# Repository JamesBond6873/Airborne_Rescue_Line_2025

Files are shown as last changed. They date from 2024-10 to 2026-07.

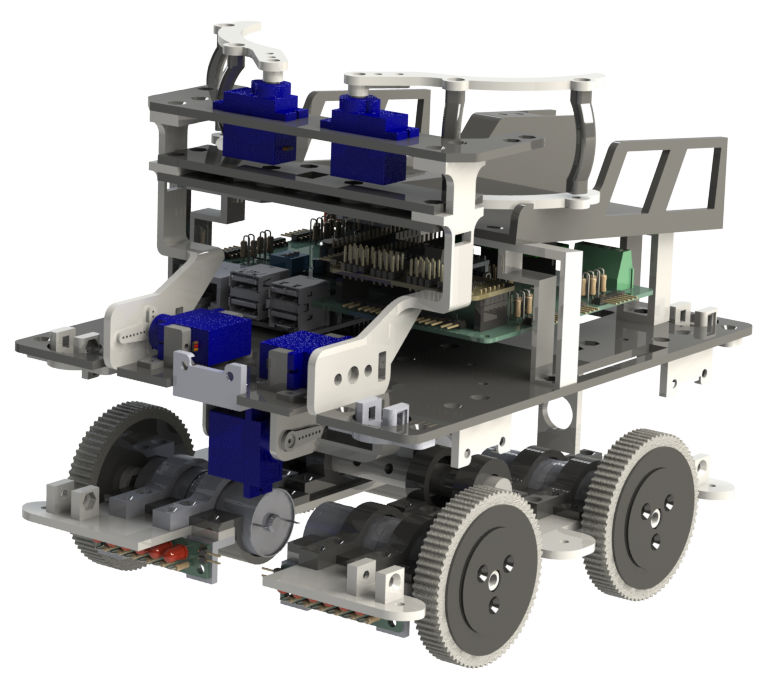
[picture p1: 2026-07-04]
Hardware/CAD/3D_Model_Pictures/Wall-E_3D_Model_Right.png

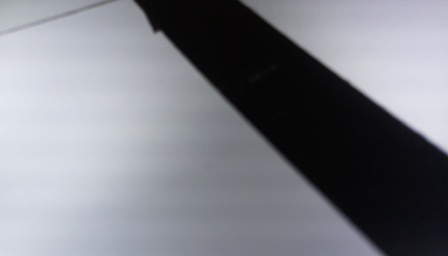
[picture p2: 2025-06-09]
SwTest/Image (122).jpg

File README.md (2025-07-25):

<div align="center">
  <a href="https://github.com/JamesBond6873">
    
  </a>
  
  <a href="https://github.com/eumesmodefacto">
    
  </a>
</div>

<br/>

<p align="center">
  This is the repository for <strong>Airborne</strong>, a Portuguese robotics team that participated in the
  <a href="https://junior.robocup.org/">RoboCup Junior</a> sub-league
  <a href="https://junior.robocup.org/rcj-rescue-line/">Rescue Line</a>.
</p>

# About the Competition
<p align="center"><i>
  "The land is too dangerous for humans to reach the victims. Your team has been given a challenging task. The robot must be able to carry out a rescue mission in a fully autonomous mode with no human assistance. The robot must be durable and intelligent enough to navigate treacherous terrain with hills, uneven land, and rubble without getting stuck. When the robot reaches the victims, it has to gently and carefully transport each one to the safe evacuation point where humans can take over the rescue. The robot should exit the evacuation zone after a successful rescue to continue its mission throughout the disaster scene until it leaves the site. Time and technical skills are essential!"
</i></p>

<div align="center">
  
</div>

# About the Robot

<!-- First block: Image on the left -->


<p align="justify">
  Our robot was built to reliably complete all challenges of the RoboCup Junior Rescue Line competition through a combination of computation, custom electronics, and mechanical design. It uses a dual-processor architecture: a Raspberry Pi 5 for high-level logic and AI, and a Raspberry Pi Pico for real-time control of motors and sensors. A Google Coral USB Accelerator enables onboard execution of two YOLOv8 models, one for victim detection and another for identifying the silver evacuation zone, which provide fast and accurate results compared to traditional computer vision.
</p>

<br/>

<!-- Second block: Image on the right -->


<p align="justify">
  The chassis was entirely designed in SolidWorks and 3D printed, with over 70 custom parts and a modular structure that simplifies maintenance. A tilt-mounted wide-angle camera, passive suspension system, and dual-servo rescue arm ensure strong performance across rough terrain. Internally, custom PCBs manage power distribution and sensor integration, keeping the system reliable and clean, with a much lower risk of lose wires. Software processes run in parallel for serial communication between boards, image processing, and control/decision-making, supported by a custom HTML/Websocket interface for real-time monitoring and debugging.
</p>

<br/>

<p align="center">
  As required by the competition <a href="https://github.com/JamesBond6873/Airborne_Rescue_Line_2025/blob/main/Documents/Rules/000_RoboCup_Junior_Rescue_Line_Rules_2025.pdf">rules</a>, in addition to this GitHub Repository, we created detailed documentation of the robot and our development process in the form of a <a href="https://github.com/JamesBond6873/Airborne_Rescue_Line_2025/blob/main/Documents/Final%20Rubrics/00_Airborne_TDP_RoboCup_Rescue_Line_2025.pdf">Technical Description Paper</a>, a <a href="https://github.com/JamesBond6873/Airborne_Rescue_Line_2025/blob/main/Documents/Final%20Rubrics/01_Airborne_Poster_RoboCup_Rescue_Line_2025.pdf">Technical Poster</a>, and a <a href="https://github.com/JamesBond6873/Airborne_Rescue_Line_2025/blob/main/Documents/Final%20Rubrics/02_Airborne_Video_RoboCup_Rescue_Line_2025_Compressed.mp4">Presentation Video</a>.
</p>

## 📂 Components

- Raspberry Pi 5 8GB Ram
- Raspberry Pi Pico
- Google Coral USB Accelerator
- Raspberry Pi Camera Module V3 Wide
- 5x VL53L0X ToF
- ICM-20948 9DOF IMU
- TCA9458 Multiplexer
- 4x Home-made Silicone Wheels
- 4x 12V 77RPM DC Geared Motors
- 4x 3S ESCs
- 6x SG90 MicroServos
- PCA9685 Servo Driver
- 2x Custom Led Bar PCB
- DRV8833 Power Driver
- Gens Ace 3S 2700mAh Lipo Battery
- D24V50F5 Step Down
- D36V28F5 Step Down

<br/>

## 🧠 Repository Structure

<p align="justify"> 
  This repository contains all the files developed and used throughout our RoboCup Junior Rescue Line project.
</p>

  - <code>RobotCode_Field_Version</code>: Contains the latest version of the code used in the official Field Runs
  - <code>RobotCode_TC_Version</code>: Contains the version used during the Technical Challenge run
  - <code>Ai</code>: Contains the versions of the YoloV8 Small Models used for victim and silver strip detections
  - <code>Documents</code>:
      - <code>Final Rubrics</code>: Contains our final three evaluated documents: Team Description Paper, Technical Poster and  Presentation Video (compressed)
      - <code>Rules</code>: Contains all official competition rulebooks (Rescue Line, Technical Challenge, SuperTeams), as well as the corresponding rubrics and templates for the documents
      - <code>scores</code>:  Contains the final scores from the RoboCup Junior World Championship 2025, in Salvador, Brazil

<br/>

# 🔗 Useful Links

- [Airborne Photo/Video Album](https://drive.google.com/drive/folders/1JC7H4FIJUuHvwdzJ9MUNMwsvkezMXKDg?usp=drive_link)
- [Technical Description Paper](https://drive.google.com/file/d/1SsVflj773ZcgajpcdkzmWjwUXBWZYv1-/view?usp=drive_link)
- [Technical Poster](https://drive.google.com/file/d/1fPJXqmR9CHxOLH45z3VVppOXiR5PiPfq/view?usp=drive_link)
- [Presentation Video](https://drive.google.com/file/d/1rCQD-FLG8RNpqSPlJDvGeZCaVhfCN_2y/view?usp=drive_link)
- [Rescue Line Rules 2025](https://github.com/JamesBond6873/Airborne_Rescue_Line_2025/blob/main/Documents/Rules/000_RoboCup_Junior_Rescue_Line_Rules_2025.pdf)
- [Airborne Instagram Account](https://www.instagram.com/airborne_2023/)

<br/>
<br/>

# 🤝 Sponsors



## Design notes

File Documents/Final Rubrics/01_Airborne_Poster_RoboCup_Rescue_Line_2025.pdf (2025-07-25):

# Team

## Team Captain; Lead Programmer; Electronics & PCB Design; Ai

## Francisco Gaspar

I’m Francisco, and I’ve been leading the team since the start in 2022. I designed our custom PCBs and handled most of the programming, from low-level control to AI integration. I trained and deployed our YOLOv8 models and built the logic that helps the robot make decisions on the field. I love solving problems by mixing hardware and software.

## André Pinto

## Team Co-Captain; 3D modelling; Sponsorship Manager

I’m André, and I focused on designing the robot’s structure. I created all the 3D models in SolidWorks and made sure everything, from suspension to the camera tilt mechanism, fit and worked reliably. I also took care of getting sponsorships and managing our budget. I really enjoy the mechanical side of things and making sure we’re prepared both on and off the field.

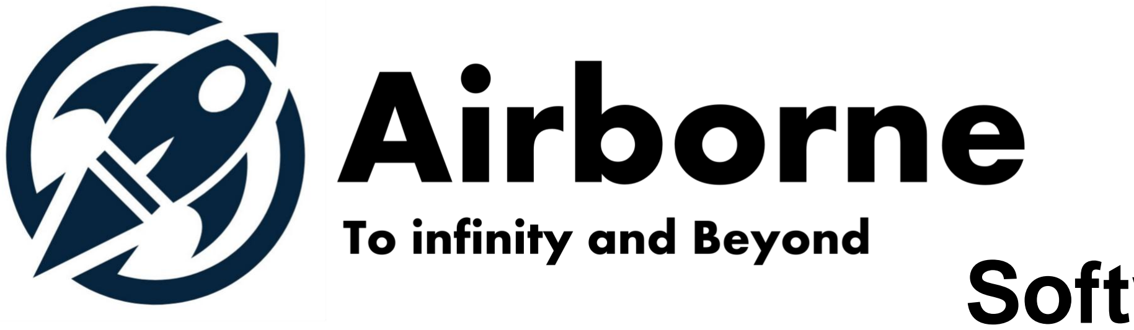
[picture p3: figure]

Airborne Robotics was founded in 2023 with the goal of building a CanSat for the national competition. Nevertheless, we ended up competing
in | our | first | Robotics | National
Championship (FNR 2024), securing 1

st Place and qualifying for the European Championship in Germany. Although our results weren’t perfect,
the | experience | motivated | us | to
completely redesign the robot from the ground up. In 2025, with a new dual-processor architecture and our first reliable custom PCBs, we won 1st place at the National Championship Rescue Line Competition, earning us a
spot | at | the | RoboCup | World
Championship in Brazil.

European Championship 2024

National Robotics Festival 2025

1

st Place FNR 2024

1

st Place FNR 2025

## Raspberry Pi Pico

Chosen for its versatility and general compatibility; responsible for sensor and actuator integration

## Raspberry Pi 5

Main computing device,
responsible for image
processing and decision
making

## Raspberry Pi Camera Module V3 Wide

Used to acquire visual
data; main sensor

## TCA9458 Multiplexer

Responsible for integrating

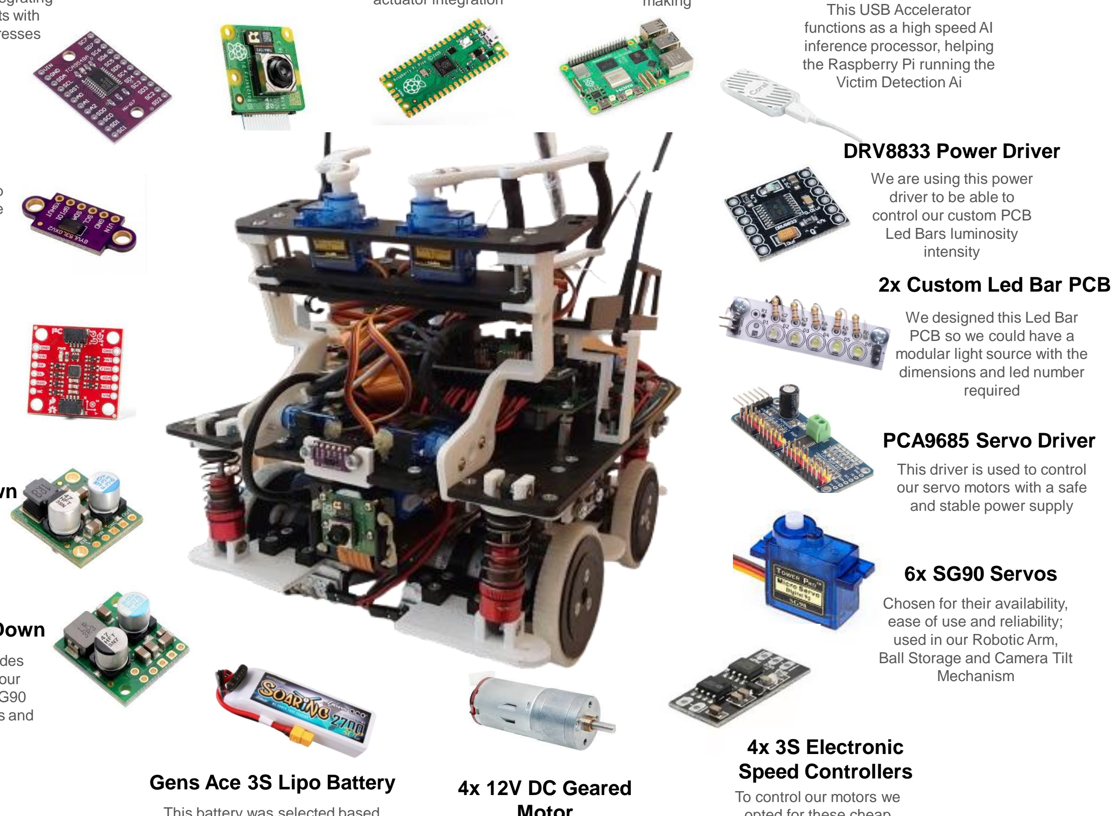
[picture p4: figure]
Gens Ace 3S Lipo Battery; 4x 12V DC Geared; 4x 3S Electronic Speed Controllers; To control our motors we; This USB Accelerator functions as a high speed AI inference processor, helping the Raspberry Pi running the Victim Detection Ai; DRV8833 Power Driver; We are using this power driver to be able to control our custom PCB Led Bars luminosity intensity; 2x Custom Led Bar PCB; We designed this Led Bar PCB so we could have a modular light source with the dimensions and led number required; PCA9685 Servo Driver; This driver is used to control our servo motors with a safe and stable power supply; 6x SG90 Servos; Chosen for their availability, ease of use and reliability; used in our Robotic Arm, Ball Storage and Camera Tilt Mechanism

the Time of Flights with
different I2C addresses

## 5x VL53L0X Time of Flights

These ToFs are used to
detect obstacles and help
guide the robot during the evacuation zone

## ICM-20948 9DOF IMU

The Inertial Measurement
Unit is used to acquire 3D data of acceleration and
rotational speed to estimate robot pitch (ramp inclination

## D24V50F5 Step Down

This step down provides
stable power (5V; 5A) to
our Raspberry Pi 5

## D36V28F5 Step Down

This step down provides
power (5V; 3.2A) to our
Raspberry Pi Pico, SG90
Servos, Time of Flights and IMU

This battery was selected based on their capacity, power output and dimensions

## Motor

These motors were chosen
because of their remarkable power at a decent speed

opted for these cheap
electronic speed controllers

## Google Coral USB Accelerator

# Hardware

Our robot’s chassis was entirely designed in SolidWorks and manufactured using FDM 3D printing with standard PLA, chosen for its rigidity and ease of use. The design features over 70 components, including 30+ unique parts, assembled into a compact 25×20×20 cm frame. Its modular three-level structure – dedicated to victim recovery; sensors & logic; actuation – makes it easy to access, repair, and upgrade. Rounded corners and a low center of mass ensure smooth movement across ramps and more complex terrain.

## Robot Chassis

To improve traction and durability, we implemented a passive suspension system: the bottom layer is split into two floating halves connected by bearings and flexible dampers. This allows the chassis to adapt to uneven surfaces and reduces shock from obstacles. The system ensures four wheels almost always stay grounded, improving stability over elements like speed bumps, debris or toothpicks.

## Passive Suspension

We designed and soldered two custom PCBs in-house: the Main Control PCB and the Custom LED Bar PCB. The Main PCB integrates the Raspberry Pi 5 and Pico with ESCs, sensors, power rails, and peripherals using clean, socketed connectors. It includes RGB LEDs, a buzzer, and DIP switches for debugging and runtime configuration. The LED Bar PCB drives high-brightness RGB LEDs using a repurposed DRV8833 motor driver for efficient, noise-free illumination.
Both boards were developed using a test-driven approach and are currently on their fourth revision and second versions, respectively. Their compact layout and reliable connections play a key role in simplifying internal wiring, reducing noise, and ensuring system stability.

## Custom PCBs

To reduce complexity and improve versatility, our robot uses a single wide-angle camera mounted on a tilt mechanism driven by a lightweight SG90 servo. This design replaces the typical dual-camera setup, avoiding fragile second flat cables and saving space.
The servo adjusts the camera’s angle during a run, improving performance on slopes and allowing the robot to anticipate line gaps by gradually tilting forward. This flexible vision system improves reliability and makes the robot more adaptable to dynamic field conditions.

## Camera Tilt Mechanism

# Software

bstac e etecte b ront o

wo reen ar ers etecte

a | etecte | no
v s b e ne r | t a ter etect on ne
e | ne etecte
b re conto r
ver ne etecte b | I
t c | etecte b ma e
| s m ar t
am etecte b | cce erat on ector
am | own etecte b | cce erat on ector
to | otors
everse a n stra | t at t e to o ne o nt

camera orwar move
orwar nt an new
ne
otate | e rees s n a t mer an ass r n t e ne s etecte reverse a b t
r ve aro n n a
c rve nt a new ne
s etecte base on
s ewa s o stances

to motors or
secon s t en move
orwar a a n

et b ect ve to
one an a n
stra | t at t e to o
| ne

everse

Increase base ne motor s ee oc s

ma e rocess n
c oser to t e ma e

ecrease base ne motor s ee t t

camera | to et w er ma es
ac o | ro ress
sw tc s act vate

rn t e robot accor n
to t e c rrent center n
var ab e
eset tate ar ab es an rn | obot | ts
es | es | es | es | es

es

es

es

es

o

o | o | o | o

o

o

o

o

## Line Following

Is tar et va

re | v ct ms e os te Is tar et a | ct m

re a v ct ms
co ecte | ea | to e os t

Is t ere no wa to
t e s e or b ac n
ront
Is t a va | e t
oa | I | o e | r entate at t e e t an | r ve o t
ec | b ect ve tat s

et ob ect ve to
n | ct ms
n | ct m etect on
In erence on a t re | rame
eterm ne t e b | est o n n | o
otate to ne | e
rn an | r ve
towar s t e tar et
c | ct m an | ace n
t e correct stora e s e

et ob ect ve to
e os t | ct ms
otate | e rees an m b ac s ver v ct ms
r ve aro n t e e | e o t e evac at on one

et ob ect ve to
t

et reen re corner
conto rs an var ab es

es

o

o | o

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
n ct m

e os t ct m

t

## Evacuation Zone

## Line Following Algorithm

Our robot’s line-following algorithm is based on a seven-point of interest (POI) system that analyzes each frame captured by a wide-angle camera. The camera feed is cropped to a horizontal strip closer to the bottom of the image, where the line is closer to the robot, allowing faster and more relevant processing. From both the full image and the cropped region, the algorithm identifies the leftmost, rightmost, and highest points on the black line. Additionally, the lowest point is considered from the full image. These seven POIs give the robot multiple options for determining the best path forward.

This method, originally introduced by team OverEngineering²,
was further improved by us with a sharp-turn biasing system.
When the robot detects turns sharper than 90 degrees, it
adjusts its path planning accordingly. Even if the POI location appears visually similar to a gentler turn. This added logic greatly improves the robot’s ability to maintain the line in complex tile configurations. In most cases, the robot follows the highest POI in the cropped region for stable and predictive steering. This approach has proven both fast and reliable, and it handles sudden directional changes better than traditional centroid/moments-following methods.

To handle critical vision tasks with higher reliability, we trained two custom YOLOv8 small models, both running in real time on a Coral USB Accelerator. The first model is responsible for victim detection in the evacuation zone. This model was trained on a dataset of over 3,000 labeled instances from more than 1,000 annotated images collected during tests and the 2025 national competition.
The second YOLOv8 model detects the silver strip at the entrance of the evacuation zone. This model was trained on over 6,000 labeled examples across 2,000+ images, helping the robot recognize the zone entrance with much greater consistency.

## Yolo AI Models

To simplify debugging and better understand the robot’s behavior during tests, we developed an innovative WebSocket-based monitoring system. A dedicated process on the Raspberry Pi updates a set of predefined variables at 20 Hz, which can be accessed remotely from our computers. These values are displayed on a custom HTML page designed to replace the traditional console output with a more readable and organized interface.
Although still a work in progress, this tool has already proven extremely useful for logging and real-time analysis, helping us identify bugs, monitor internal states, and tune parameters more efficiently.

## WebSocket and HTML Page

Python: Python served as the backbone for our high-level logic and image processing tasks. Its simplicity and extensive libraries made it ideal for rapid development and handling complex computations. Libraries like OpenCV and NumPy enabled advanced vision capabilities crucial for our robot’s performance.

Visual Studio Code: We used Visual Studio Code paired with Remote SSH to seamlessly develop and debug code directly on our Raspberry Pi. This setup allowed editing and testing in a Linux environment while maintaining access to powerful development tools and a direct integration with GitHub. Additionally, by having a raspberry pi standing alone, we could program the robot without being close to it.

Arduino IDE: The Arduino IDE was our choice for programming the Raspberry Pi Pico in C++. Its user-friendly environment and robust library support simplified sensor interfacing and actuator control. Using Arduino IDE, we implemented real-time hardware communication and control critical to the robot’s responsiveness.

## Sponsors:

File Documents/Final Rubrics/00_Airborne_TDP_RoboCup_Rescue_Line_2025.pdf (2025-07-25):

## ROBOCUPJUNIOR RESCUE LINE 2025

## TEAM DESCRIPTION PAPER

## Airborne

André Pinto and Francisco Gaspar

Contents

1

Abstract

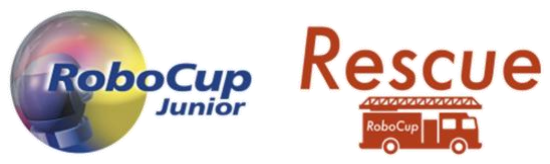
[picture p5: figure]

Our robot was designed to reliably complete all challenges of the RoboCup Junior Rescue Line competition through a combination of computation, custom electronics, and specific mechanical design. Its architecture is centered on a dual-processor setup: a Raspberry Pi 5 handles high-level logic and AI inference, while a Raspberry Pi Pico manages real-time motor and sensor control. A Google Coral USB Accelerator allows onboard execution of two YOLOv8 AI models, one for victim detection and another for identifying the silver evacuation zone entrance, outperforming traditional computer vision methods in accuracy and speed.

The robot’s chassis, fully designed in SolidWorks and 3D printed, features over 70 custom parts and a modular architecture that simplifies maintenance and upgrades. A tilt-mounted wide-angle camera, passive suspension system, and dual-servo rescue arm provide great performance on complex terrain. Custom PCBs, developed in-house, manage power, sensors, and actuators while keeping internal wiring clean and reliable. The software runs in parallel processes for camera input, sensor reading, and decision-making for fast and consistent performance. A custom HTML interface, powered by a WebSocket server, allows real-time monitoring and debugging. The result is a fast, reliable, and intelligent system engineered to perform at high level across all stages of Rescue Line.

### 1. Introduction

a. Francisco Gaspar
Team Captain; Lead Programmer; Electronics & PCB Design; AI

I am Francisco, and I have been leading the team since the start in 2022. I designed our custom PCBs and handled most of the programming, from low-level control to AI integration. I trained and deployed our YOLOv8 models and built the logic that helps the robot make decisions on the field. I love solving problems by mixing hardware and software.

b. André Pinto
Team Co-Captain; 3D Modelling & Structure; Budget & Sponsorship Manager

I am André, and I focused on designing the robot’s structure. I created all the 3D models in SolidWorks and made sure everything, from suspension to the camera tilt mechanism, fit and worked reliably. I also took care of getting sponsorships and managing our budget. I really enjoy the mechanical side of things and making sure we’re prepared both on and off the field.

### 2. Project Planning

a. Overall Project Plan

Objective: Our team's primary objective for the RoboCup Junior Rescue Line League competition is to design and build a robot capable of navigating the rescue scenarios efficiently and reliably. To achieve this, we have outlined several key requirements and constraints that our robot and team must meet, based on the competition rules and the physical and time deadlines inherent to the event, Table 1.

Requirement | Tools/Components | Final Solution
Navigate and turn within the 25x25x25 (cm) space in between pillars | Custom 3D Model; 12V DC Motors paired with ESCs | We designed a compact 3D printable chassis with dimensions smaller than the ones required for ease of navigation. Also benefits having a lower center of gravity
Overcome speed bumps, ramps and seesaws | Silicone Wheels (traction); IMU ICM-20948 (ramp detection) | The robot has high-traction custom made silicone wheels and a low center of gravity for stability. It uses a hard suspension setup to soften the load on 3D printed parts during high impact situations
Follow the black line; detect green intersection markers and red strip | Raspberry Pi Camera Module V3 Wide; Raspberry Pi 5; Raspberry Pi Pico | We chose a camera as it was the sensor with less limitations and a lot of possibilities, being able to deal with multiple tasks solely relying on it. More specifically, we chose the Raspberry Pi Camera Module V3 Wide. The camera is mounted on a tilt platform that points down on Line Following and forward on the Evacuation Zone
Detect and work around obstacles | Time of Flight VL53L0X | With the use of time of flights (ToFs) we are able to detect any object that is in front of the robot. After detection we can move around it based on side-pointing ToFs.
Detect reflective silver strip at the entrance of the evacuation zone | USB Google Coral TPU; Raspberry Pi Camera Module V3 Wide | After attempting multiple traditional camera algorithms, we decided on using a YoloV8 small classification model, trained on a custom dataset for the silver strip detection. The values are averaged out over a period of time to prevent false positive from new scenarios for the model
Detect victims and evacuation points | USB Google Coral TPU; Raspberry Pi Camera Module V3 Wide | A YoloV8 small detection model trained on a custom dataset was our final solution, as it proved itself to be much more reliable than OpenCV Hough Transform for Circles with basic color detections.
Pick, store and deposit victims | SG90 Servos (Robotic Arm & Ball Storage) | The robot has a robotic arm that is deployed once a ball is within reach. This arm is capable of sorting the balls to different compartments according to their color/status. We opted to have a ball storage capable of storing a total of 4 balls.
Handle and Lack of Progress Procedure | Lack of Progress ON/OFF Switch | As the robot is already quite tall and has a complex 3D design, we chose to incorporate a flexible handle made out of zip-ties. Additionally, we have a main power switch for quick power offs and a Lack of Progress switch.

Table 1: Overview of Requirements and Final Solutions for Rescue Line

Project Schedule: Right after our participation in the European Championship in June 2024, Germany, we decided that we wanted to try rescue line for another year. So, as soon as we finished our final exams, we started planning and preparing. With the plan of what needs to be changed, added and improved, we created a schedule for the year, that can be seen in Figure 1.

For the start of the year, we were able to stay relatively close to the schedule we had set up previously. Unfortunately, due to some problems with our power driver choices and camera positioning, we ended up taking longer than expected trying to integrate some software solutions because the robot was not as responsive as expected. Eventually, we caught up to the schedule with the majority of the problems solved.

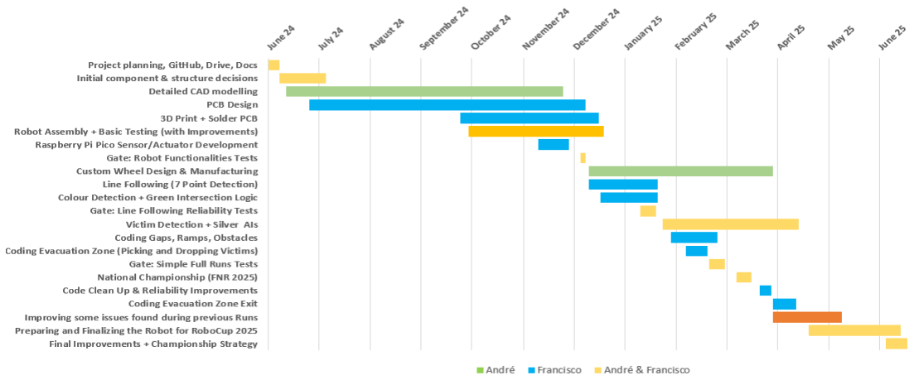
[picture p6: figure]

Figure 1: Gantt Chart of our Project Schedule

b. Integration Plan

According to the requirements of this competition, defined in Table 1, we designed our robot with the integration of specific sensors and components to meet those expectations. Each component we integrated underwent a selection of two main phases. The first was a testing phase, during which we developed a simple setup to evaluate and try out whether the component could reliably perform the required functionalities. If it met our expectations, we proceeded to the second phase: integrating the component into the main system. This included implementing the necessary code in the main program and conducting further validation tests such as compatibility in between sensors. An explanation of how each component addresses the competition requirements is presented in Table
1. The overall architecture, including connections and interactions between components, is illustrated in Figure 2.

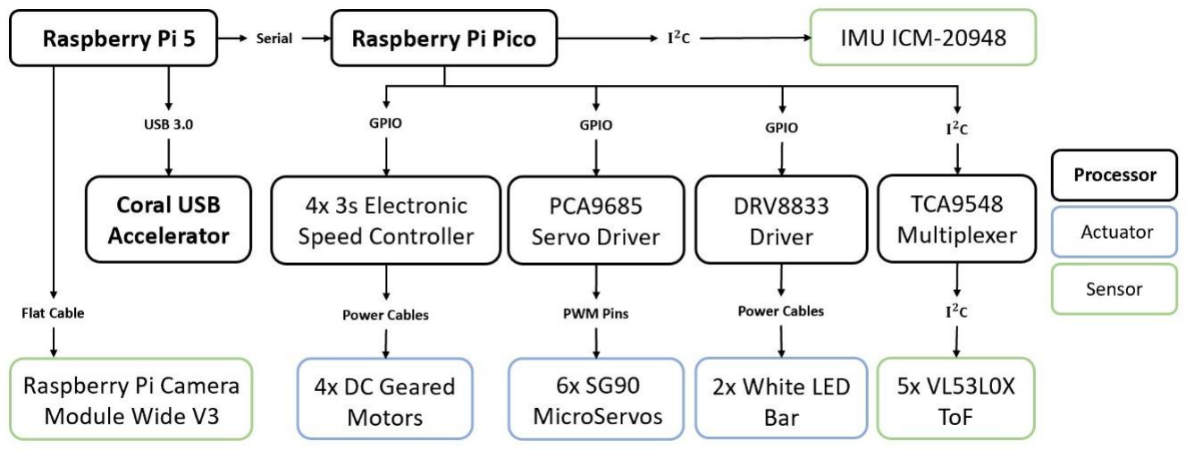
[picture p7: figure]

Figure 2: Integration Plan

### 3. Hardware

Our robot hardware was designed to be fully custom and as much as possible home-manufactured. We opted to design and 3D print the entire structure, enabling a chassis tailored specifically for this competition, with optimized sensor placement, robustness, and modularity in mind. This approach also allows for rapid replacement of individual components when necessary.

Based on the requirements outlined in Table 1, we selected the components shown in the hardware diagram (Figure 3). We then designed the full CAD model of the robot and a Custom PCB, ensuring that all connections are both mechanically stable and easily removable for maintenance/replacement. As a result, our robot features a modular three-level hardware architecture, assemble with screws and developed to prioritize stability and reliability. Each level corresponds to a specific electro-mechanic, computational or mechanical subsystem and collectively contributes to the robot’s effectiveness in the Rescue Line environment.

The lower level contains the drive train system, composed of four 12V DC motors with custom silicone wheels, and is designed with a central axis that allows left or right side tilting to improve maneuverability. The middle level houses the core electronics, including the Raspberry Pi 5, a custom PCB, and the Google Coral, and supports the servo-driven arm used to manipulate victim balls. Finally, the top level integrates a dual-compartment storage system with a servo-controlled gate to sort and release balls based on classification.

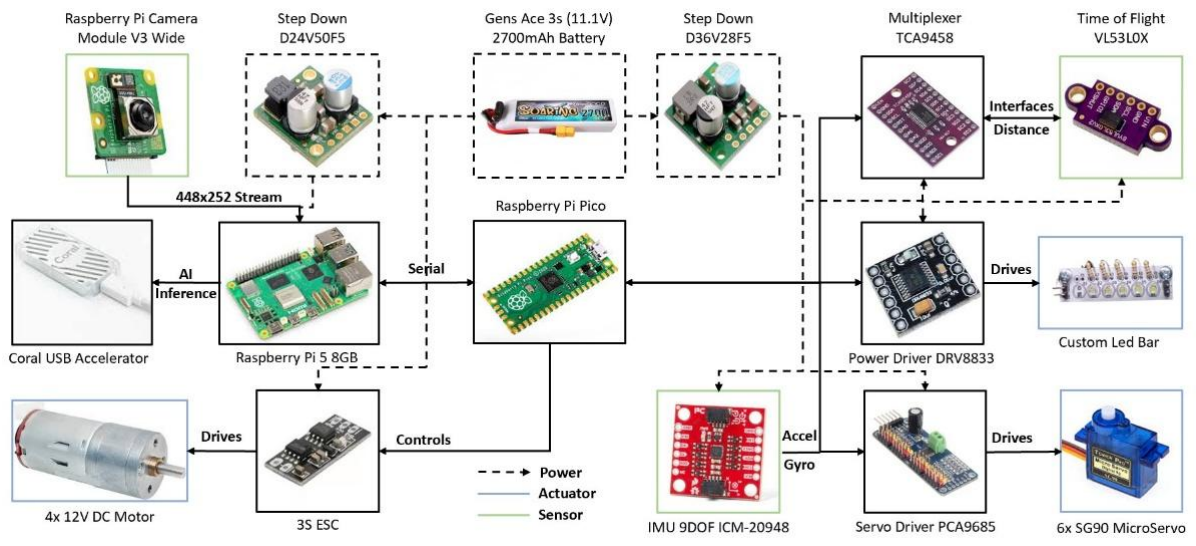
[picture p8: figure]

Figure 3: Hardware Diagram

a. Mechanical Design and Manufacturing

Robot Chassis: Our robot's chassis and all mechanical components were fully designed in SolidWorks, allowing for tight integration of submodules and optimization of internal space. All structural parts were manufactured using FDM 3D printing with PLA filament, chosen for its simplicity and mechanical strength. The design comprises over 30 unique 3D-printed parts, totaling more than 70 components. This modular architecture based on many small parts allows easy maintenance and upgrades, as individual parts can be replaced and redesigned without affecting the full assembly.

The robot has compact dimensions of approximately 25 × 20 × 20 cm, weighing 1.8 kg. This compact size and low center of mass, provide strong stability on ramps, seesaws, and speed bumps. The robot has rounded corners to prevent getting stuck on pillars and the zone entrance/exit. The structure prioritizes function over aesthetics, featuring a simple zip-tie handle for flexible handling during testing and setup. All design decisions were driven by the requisites on table 1. See the full CAD chassis design and the fully built robot in Figure 4.

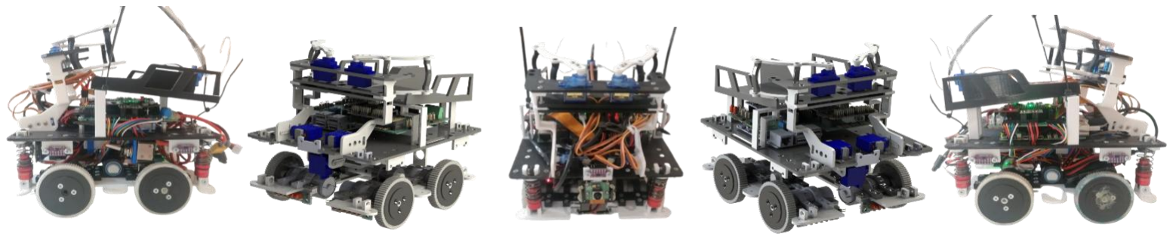
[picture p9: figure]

Figure 4: Robot Chassis Design Rendering and Fully Finished Robot

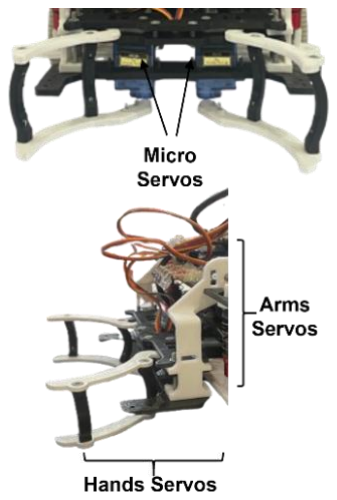
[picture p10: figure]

Rescue Mechanism: Our rescue arm is mounted on the second level of the robot and is controlled via SG90 micro servos, selected for their availability, light weight, and ease of use. The arm is designed to grasp and lift spherical victims, using a dual-servo gripping mechanism that adjusts the claw width during operation. While no encoder-based feedback system is in place, the mechanical simplicity ensures repeatable and reliable pickups within the expected rescue area dimensions.

The actuation mechanism has been fine-tuned to ensure smooth release without high acceleration movements and minimal accidental drops. Additionally, the robotic arm is able to position the balls on the left or right storage side, therefore
allowing it to sort between alive and dead victims.

Suspension System: To tackle uneven terrain such as speed bumps and debris (see Table 1), we developed an innovative passive suspension system that enhances both stability and durability. Rather than rigidly connecting the top and bottom structural levels, the lower plate is split into two independent sections (left and right), each able to tilt forward and backward via bearings. These "floating" halves (Figure 6) are connected to the main chassis using semi-flexible dampers, allowing vertical displacement and increased flexibility. This setup ensures that almost always four wheels remain in contact with the ground, even on irregular surfaces. Beyond improving traction and obstacle traversal, the suspension absorbs shocks that previously caused mechanical failures — notably, the main axle’s connection to the frame. In testing over rice, toothpicks, plastic fragments, and speed bumps, it significantly reduced vibration and preserved structural integrity.

Figure 5: Robotic Arm

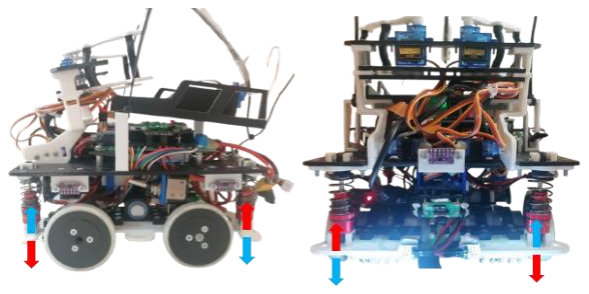
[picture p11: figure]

Figure 6: Suspension
Movement Diagram

Camera Tilt Mechanism: Instead of relying on a conventional setup with two rigidly mounted cameras, we designed our robot with a single camera mounted on a tilt mechanism (see Figure 7). This innovative solution allows us to dynamically adjust the viewing angle based on the robot’s current situation, compensating for ramps, improving line visibility, and even enabling the robot to anticipate or skip gaps by looking further ahead.

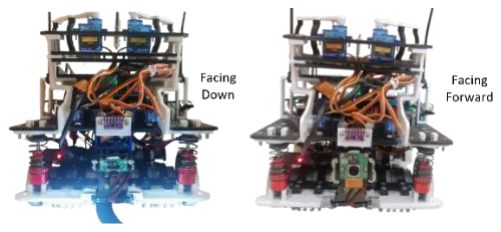
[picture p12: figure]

These design choices proved to be highly reliable during our testing. The robot operated for extended periods without overheating or wiring issues and successfully handled inclines up to 30 degrees. It also withstood small shock and collision tests, maintaining full functionality even after repeated transport and setup cycles.

b. Electronic Design and Manufacturing

Processors, Sensors and Actuators: The electronic architecture of our robot is built around a dual-processor system to balance performance with real-time reliability. We use a Raspberry Pi 5 (8GB) for high-level processing tasks such as AI inference, computer vision, and actuator output control. For responsive low-level handling, we use a Raspberry Pi Pico, which manages sensor polling and communication with actuators. These two systems are connected over a USB serial interface, ensuring robust communication while distributing computational tasks efficiently between them. A wide-angle Pi Camera streams video to the Pi 5, assisted by a Google Coral USB Accelerator for fast onboard YOLOv8 AI inference—used for both victim detection and silver line recognition.

Sensor input is provided by five VL53L0X Time-of-Flight sensors via an I2C multiplexer, and an ICM-20948 IMU for 3D acceleration and 3D rotation speed observation. Four 12V DC motors are driven by ESCs, while six SG90 servos handle the robotic arm, camera tilt, and ball storage. Two custom LED bars, controlled by a repurposed DRV8833 motor driver, ensure consistent line illumination. Power is supplied by an 11.1V LiPo battery, stepped down using two regulators to separately power the Pi 5 and all other electronics, ensuring system stability.

Custom PCBs: To ensure a compact and reliable system, we designed two custom PCBs using KiCad: the Main Control PCB and the Custom LED Bar PCB (see Figure 8). The Main PCB connects the Raspberry Pi 5, Raspberry Pi Pico, ESCs, sensors, and power rails, serving as the central hub for routing and integration. It includes easily replaceable connectors, a DIP switch for runtime configuration, and onboard RGB LEDs and a buzzer for debugging.The Custom LED Bar PCB was developed for high-brightness signaling using a DRV8833 motor driver, chosen for its ability to handle higher currents with simple digital control. The board features current-limiting resistors and precise layout to meet our size requirements.

Both boards were designed and soldered in-house, manufactured by JLCPCB. A test-driven workflow was followed, beginning with breadboard validation and progressing through schematic simulations and field testing. Our current revision, version 4, reflects multiple iterations based on integration feedback. Final validation included power stability tests, component calibration, and real-world tests across ramps and uneven surfaces. These PCBs were critical for system modularity, reliability, and clean internal wiring, directly supporting our robot’s design goals.

Figure 7: Camera
Tilt Mechanism

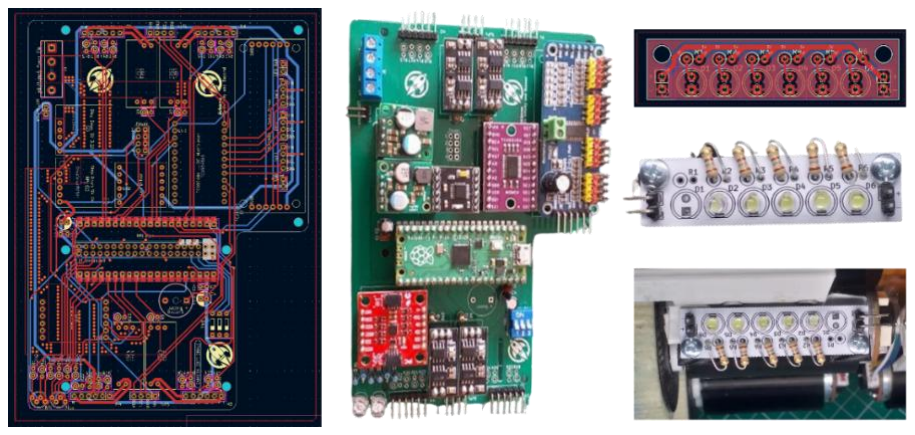
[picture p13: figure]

Figure 8: Main PCB and LED Bar PCB

To ensure electronic reliability, we conducted multiple validation tests. Battery autonomy was verified to support over 20 minutes of full operation, with voltage consistently staying above 12V to maintain motor performance. We monitored and logged voltage levels during test runs and confirmed that the system remains stable even under peak loads. Our design includes capacitors for noise reduction and protection, and both step-down converters feature built-in diodes to prevent reverse current damage.

### 4. Software

a. General Software Architecture

Our robot’s software was developed primarily in Python running on a Raspberry Pi 5, while a Raspberry Pi Pico runs C++ code to handle low-level motor and sensor control. The two communicate over USB serial. We wrote most of our code using Visual Studio Code with remote SSH into the Pi, and used GitHub for version control and WinSCP to transfer videos, images and logs. The Pico was programmed using Arduino IDE. Libraries like OpenCV and NumPy are our mainly used libraries. For object detection and classification, specifically victim recognition and silver strip, we use AI models running with the Ultralytics API, accelerated with a Coral USB TPU.

The RPi program is organized into separate processes to run tasks in parallel, see Figure 9. One handles the main camera for line following and intersection detection. A second process reads sensor data from the Pico. A third process controls the robot’s decision-making. This multiprocessing setup allows the robot to analyze visuals, collect sensor inputs, and take actions without delays or slowdowns, easily staying within the respective refresh rates.

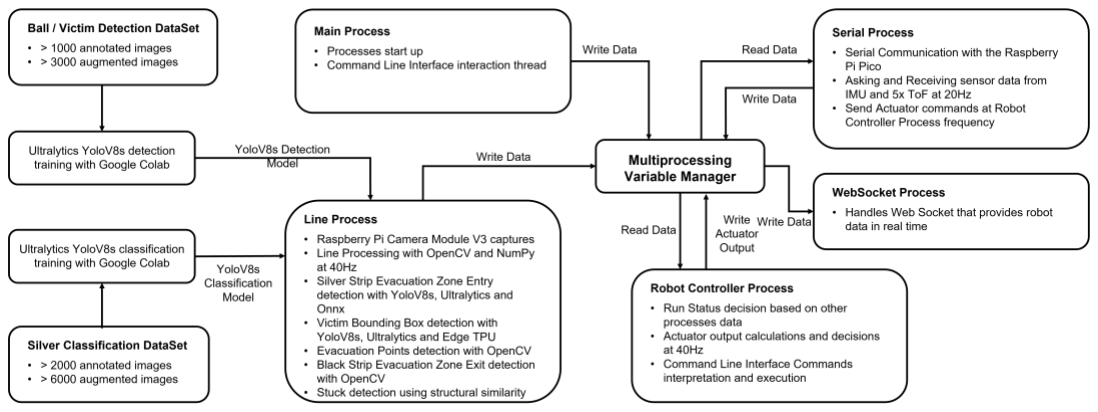
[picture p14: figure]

Figure 9: General Software Flow Diagram

Line Following: The line following is done entirely through computer vision, except for the obstacles. Images from the front-facing camera are processed in real time at 40FPS. In the figure below, Figure 10, is a simplified flowchart of our robot handles the line following, accounting for all possible scenarios described in Rescue Line Rules and requirements shown in table 1. Thanks to our custom LED bar, we reduced unidentified colors by approximately 85% with general calibration, and with environment-specific tuning, color detection accuracy reaches around 95% surpassing our reliability requirements.

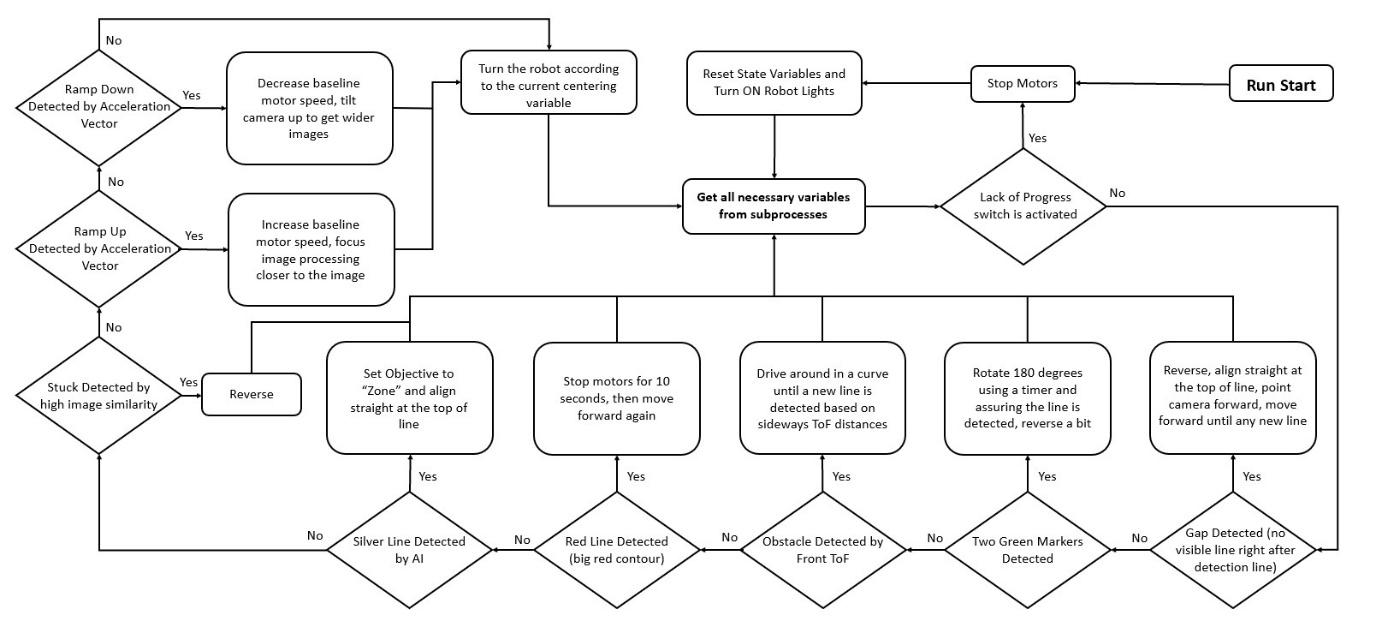
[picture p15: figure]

Figure 10: Line Following Flow Diagram

Evacuation Zone: When the robot detects a silver strip, it switches to the evacuation zone mode, shown in Figure
11. The tilt mechanism points the camera forward, the line following lights are turned off (helps with Victim Detection AI), and the software searches for silver and black balls. A YOLOv8s model detects the balls, allowing the robot to collect and sort the silver and black balls. Our strategy is to first collect all victims before delivering them, but if the situation gets difficult, meaning we are in the evacuation zone for too long or we have used lack of progresses during it, we deposit the balls as soon as possible. To ensure reliability, we tested this system under varying lighting conditions and found that the robot detects victims with over 90% confidence in most cases.

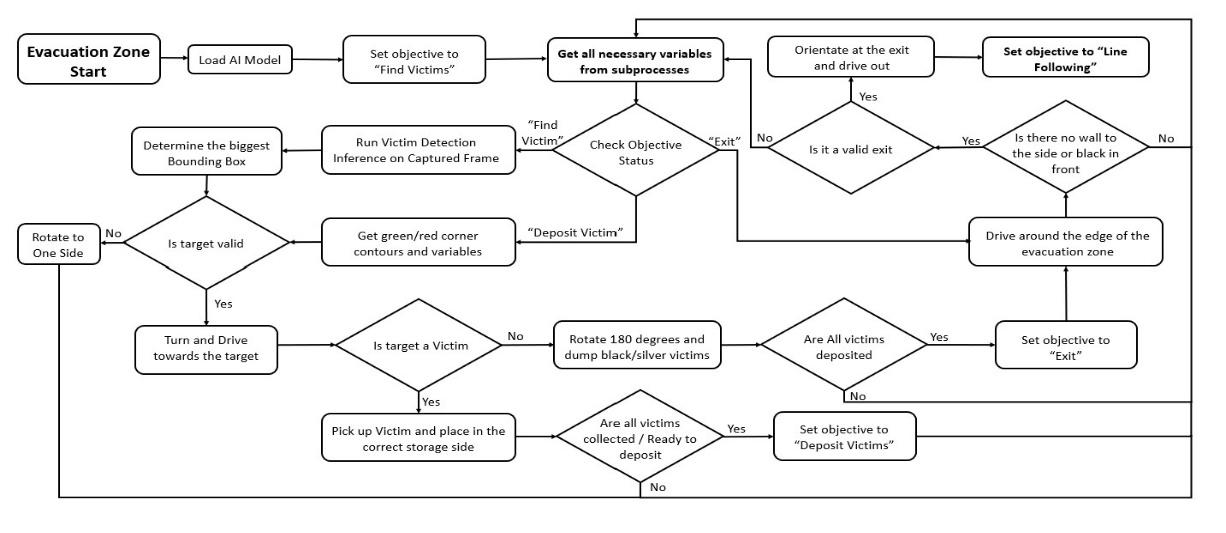
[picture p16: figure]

Figure 11: Evacuation Zone Flow Diagram

b. Innovative Solutions

Line Detection: Our line detection algorithm relies on a seven-point of interest (POI) system to determine the position and direction of the black line in each frame (see Figure 12). Inspired by a method first introduced by team Overengineering², we expanded on it by adding an extra directional bias for sharp turns. This means that turns sharper than 90 degrees are treated with increased weight, even when the chosen POI lies on the image’s edge in both standard and sharp turn cases. This adjustment significantly improved reliability. The robot uses a wide-angle camera near the ground to capture the path ahead and selects the most appropriate POI, typically the highest one in a cropped region, for smooth steering. In Figure 12, the largest red circle shows the point the robot aims to follow.

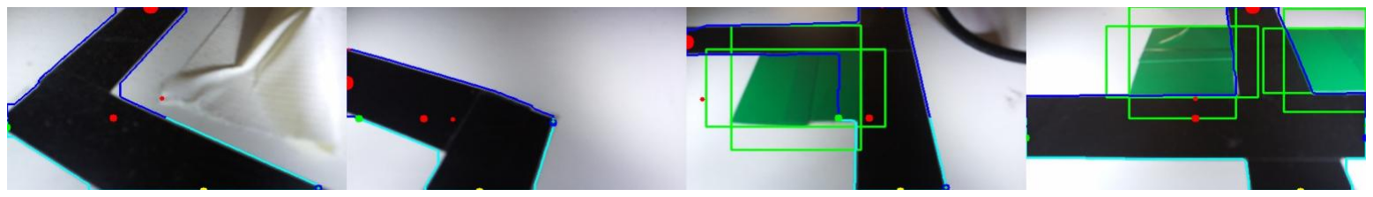
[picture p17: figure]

Figure 12: Line Detection with 7 POIs

AI YoloV8s for Victim and Silver Strip Detections: We use two custom-trained YOLOv8 small models to improve reliability in key vision tasks (see Figure 13). One model detects and classifies victims in the evacuation zone, distinguishing silver (alive) from black (dead) balls with high accuracy (around 90%), even under difficult lighting or cluttered backgrounds. The second model is used to detect the silver line at the entrance of the evacuation zone, replacing earlier OpenCV-based methods that failed under certain lighting conditions. Both models were trained using annotated datasets collected during tests and our national competition in 2025. Inference is accelerated using a Coral USB Accelerator, allowing us to run these models in real time without slowing down the rest of the system.

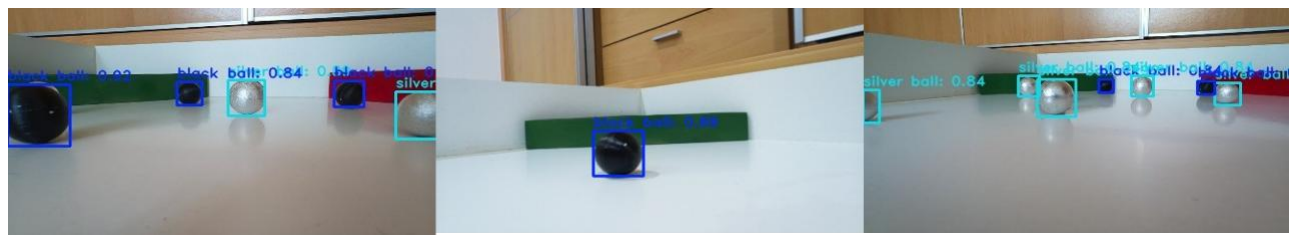
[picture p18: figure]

Figure 13: Victim Detection with YoloV8s model

WebSocket Process and HTML Page: To simplify debugging and better understand the robot’s behaviour during tests, we developed a WebSocket-based monitoring system. A dedicated process on the Raspberry Pi updates a set of predefined variables at 20 Hz, which can be accessed remotely from our computers. These values are displayed on a custom HTML page (see Figure 14), designed to replace the traditional console output with a more readable and organized interface. Although still a work in progress, this tool has already proven extremely useful for logging and real-time analysis, helping us identify bugs, monitor internal states, and tune parameters more efficiently.

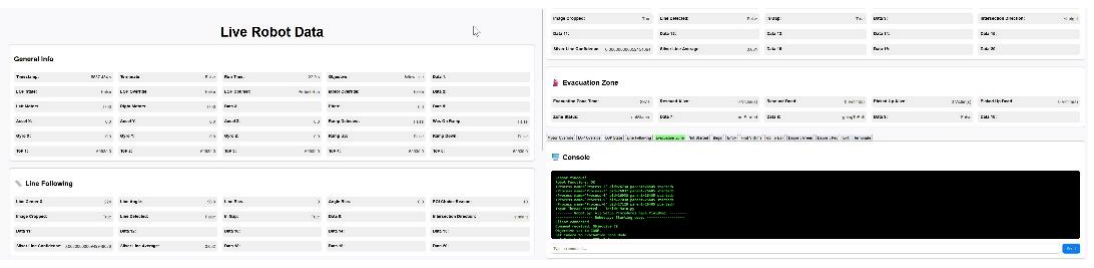
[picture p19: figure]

Figure 14: Custom HTML Page for debugging

### 5. Performance Evaluation

To ensure reliable performance under competition conditions, we carried out continuous testing throughout development. We built and maintained a growing test course, adding new challenges without removing previously working tasks. This allowed us to consistently verify that updates did not break earlier functionality. Tiles included sharp turns, tight intersections, silver markers, gaps, and ramps to test both image processing and mechanical stability.

Hardware systems like the suspension and drivetrain were tested on various surfaces, such as rice, tape, plastic, and speed bumps; to simulate difficult terrain. Ramp testing was conducted in our school gym using a large adjustable ramp to determine safe incline limits.

To improve software reliability, we developed debugging scripts and protocols. Most importantly, we can easily switch our code to Debug Mode, where instead of relying on live robot information and actuation, we use a pre-acquired dataset. Additionally, a WebSocket-based HTML interface provided live data during runs, making it easier to trace logic errors and spot unusual behavior. Screen recordings were also used to analyze edge cases and rare failures.

One significant challenge we faced was inconsistent line detection caused by variable lighting conditions across different environments. Reflections, shadows, or low contrast between the line/green markers and the floor often confused our image processing pipeline, leading to unstable navigation. To mitigate this, we designed custom LED bar PCBs to ensure uniform lighting directly in front of the camera, significantly improving reliability during line following. These lights can be toggled in software, allowing us to disable them when entering the evacuation zone, where our object detection models perform better without artificial lighting.

### 6. Conclusion

After competing at the European Championship last year and winning the national championship this season, we are proud of how far this project has come. Building everything from the ground up, from structure to software, was a challenging but rewarding journey. While no system is perfect and improvements are always possible, we are satisfied with the reliable and competitive robot we’ve created. We now look forward to the World Championship not just to compete, but to celebrate what we have built and learn from the global community.

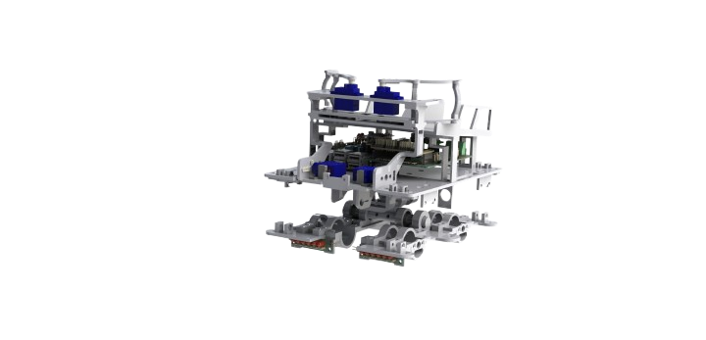
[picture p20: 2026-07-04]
Hardware/CAD/3D_Model_Pictures/Robot_3D_Model-removebg-preview.png

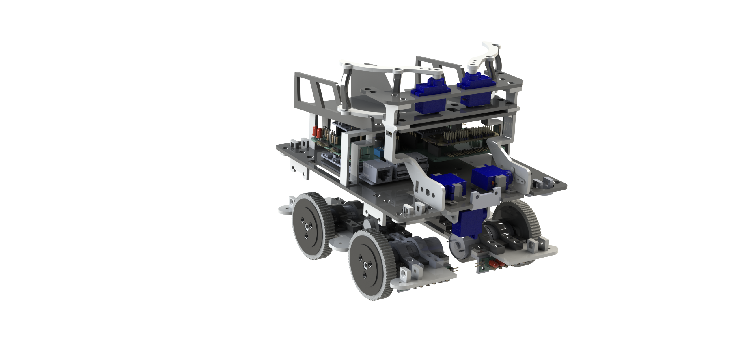
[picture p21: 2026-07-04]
Hardware/CAD/3D_Model_Pictures/Wall-E_3D_Model_Left.png

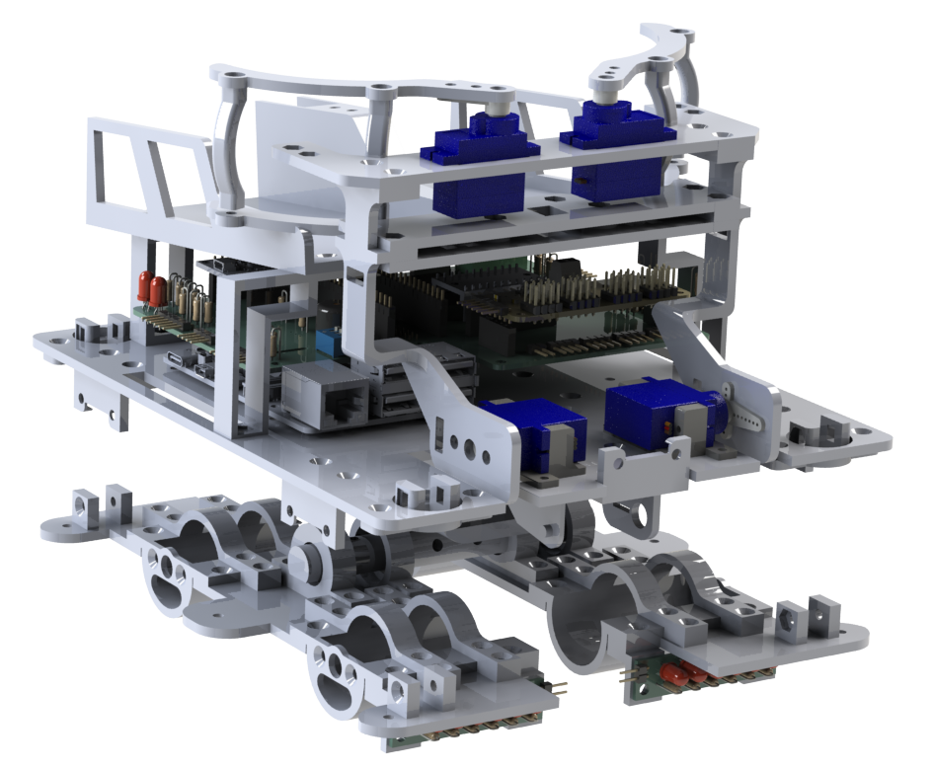
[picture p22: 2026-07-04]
Hardware/CAD/3D_Model_Pictures/Robot_3D_Model_Left.png

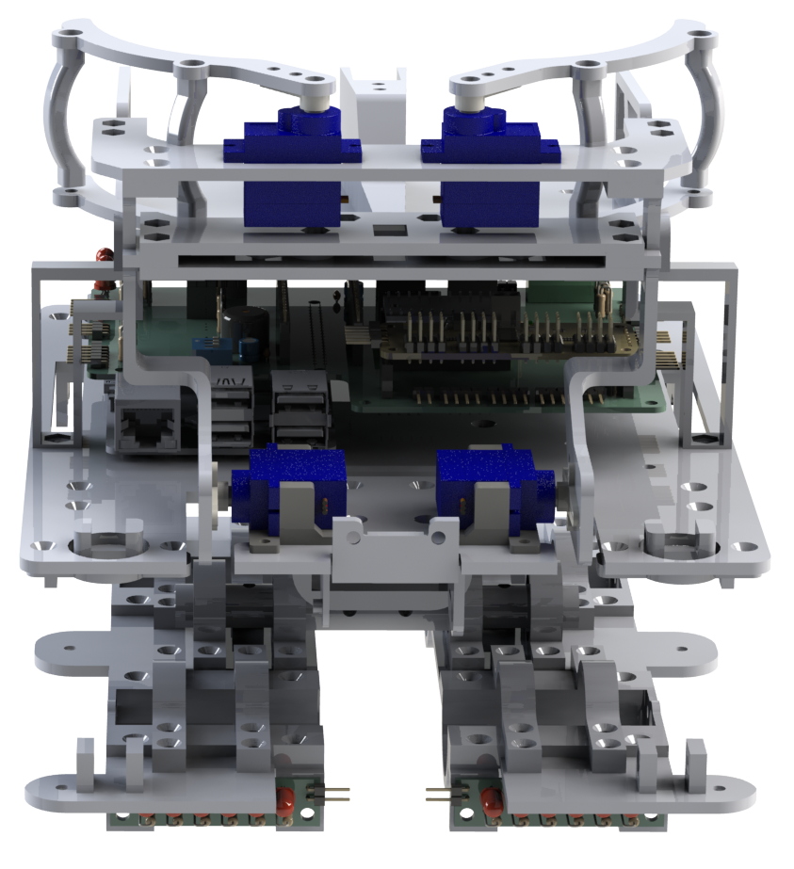
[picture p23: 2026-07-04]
Hardware/CAD/3D_Model_Pictures/Robot_3D_Model_Front.png

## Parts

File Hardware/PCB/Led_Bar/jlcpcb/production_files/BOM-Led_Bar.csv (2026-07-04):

Comment | Designator | Footprint | LCSC | Quantity
220Ω | R6 | R_Axial_DIN0207_L6.3mm_D2.5mm_P2.54mm_Vertical |  | 1
LED | D1 | LED_D5.0mm |  | 1
220Ω | R1 | R_Axial_DIN0207_L6.3mm_D2.5mm_P2.54mm_Vertical |  | 1
LED | D2 | LED_D5.0mm |  | 1
220Ω | R2 | R_Axial_DIN0207_L6.3mm_D2.5mm_P2.54mm_Vertical |  | 1
LED | D3 | LED_D5.0mm |  | 1
220Ω | R3 | R_Axial_DIN0207_L6.3mm_D2.5mm_P2.54mm_Vertical |  | 1
LED | D4 | LED_D5.0mm |  | 1
220Ω | R4 | R_Axial_DIN0207_L6.3mm_D2.5mm_P2.54mm_Vertical |  | 1
LED | D5 | LED_D5.0mm |  | 1
220Ω | R5 | R_Axial_DIN0207_L6.3mm_D2.5mm_P2.54mm_Vertical |  | 1
LED | D6 | LED_D5.0mm |  | 1
Conn_01x02 | J1 | PinHeader_1x02_P2.54mm_Vertical |  | 1
Conn_01x02 | J2 | PinHeader_1x02_P2.54mm_Vertical |  | 1

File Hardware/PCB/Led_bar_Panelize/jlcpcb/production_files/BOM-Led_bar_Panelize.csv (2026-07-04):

Comment | Designator | Footprint | LCSC | Quantity
220Ω | R1 | R_Axial_DIN0207_L6.3mm_D2.5mm_P2.54mm_Vertical |  | 1
220Ω | R5 | R_Axial_DIN0207_L6.3mm_D2.5mm_P2.54mm_Vertical |  | 1
LED | D3 | LED_D5.0mm |  | 1
220Ω | R3 | R_Axial_DIN0207_L6.3mm_D2.5mm_P2.54mm_Vertical |  | 1
220Ω | R4 | R_Axial_DIN0207_L6.3mm_D2.5mm_P2.54mm_Vertical |  | 1
220Ω | R6 | R_Axial_DIN0207_L6.3mm_D2.5mm_P2.54mm_Vertical |  | 1
LED | D4 | LED_D5.0mm |  | 1
220Ω | R2 | R_Axial_DIN0207_L6.3mm_D2.5mm_P2.54mm_Vertical |  | 1
LED | D2 | LED_D5.0mm |  | 1
Conn_01x02 | J2 | PinHeader_1x02_P2.54mm_Vertical |  | 1
LED | D6 | LED_D5.0mm |  | 1
LED | D1 | LED_D5.0mm |  | 1
LED | D5 | LED_D5.0mm |  | 1
Conn_01x02 | J1 | PinHeader_1x02_P2.54mm_Vertical |  | 1

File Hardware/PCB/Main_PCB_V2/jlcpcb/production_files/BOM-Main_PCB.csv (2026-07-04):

Comment | Designator | Footprint | LCSC | Quantity
220Ω | R2 | R_Axial_DIN0207_L6.3mm_D2.5mm_P2.54mm_Vertical |  | 1
Conn_01x02 | J6 | PinHeader_1x02_P2.54mm_Vertical |  | 1
1.2kΩ | R21 | R_Axial_DIN0207_L6.3mm_D2.5mm_P2.54mm_Vertical |  | 1
1.2kΩ | R11 | R_Axial_DIN0207_L6.3mm_D2.5mm_P2.54mm_Vertical |  | 1
2kΩ | R25 | R_Axial_DIN0207_L6.3mm_D2.5mm_P2.54mm_Vertical |  | 1
~ | IMU1 | ICM-20948 |  | 1
1.2kΩ | R9 | R_Axial_DIN0207_L6.3mm_D2.5mm_P2.54mm_Vertical |  | 1
LED_RGAB | D1 | LED_D5.0mm-4_RGB_Staggered_Pins |  | 1
1.2kΩ | R19 | R_Axial_DIN0207_L6.3mm_D2.5mm_P2.54mm_Vertical |  | 1
1.2kΩ | R7 | R_Axial_DIN0207_L6.3mm_D2.5mm_P2.54mm_Vertical |  | 1
1.2kΩ | R8 | R_Axial_DIN0207_L6.3mm_D2.5mm_P2.54mm_Vertical |  | 1
~ | ESC1 | ESCs |  | 1
~ | ESC4 | ESCs |  | 1
~ | ToF3 | ToF_VL53L0X |  | 1
Conn_01x02_Pin | J4 | PinHeader_1x02_P2.54mm_Vertical |  | 1
~ | M4 | PinHeader_Motor_Encoder |  | 1
~ | M2 | PinHeader_Motor_Encoder |  | 1
1.2kΩ | R13 | R_Axial_DIN0207_L6.3mm_D2.5mm_P2.54mm_Vertical |  | 1
~ | ToF1 | ToF_VL53L0X |  | 1
~ | ToF2 | ToF_VL53L0X |  | 1
220Ω | R1 | R_Axial_DIN0207_L6.3mm_D2.5mm_P2.54mm_Vertical |  | 1
2kΩ | R17 | R_Axial_DIN0207_L6.3mm_D2.5mm_P2.54mm_Vertical |  | 1
~ | StepDown5V5A1 | Step_Down_5V_5A_D24V50F5 |  | 1
10uF | C4 | CP_Radial_D5.0mm_P2.00mm |  | 1
1.2kΩ | R10 | R_Axial_DIN0207_L6.3mm_D2.5mm_P2.54mm_Vertical |  | 1
~ | MotorDriver2 | DRV8833 Dual Motor Driver |  | 1
100nF | C3 | C_Disc_D3.0mm_W2.0mm_P2.50mm |  | 1
SW_DIP_x03 | SW1 | SW_DIP_SPSTx03_Slide_9.78x9.8mm_W7.62mm_P2.54mm |  | 1
100nF | C1 | C_Disc_D3.0mm_W2.0mm_P2.50mm |  | 1
Battery & Power SW | J1 | Power_Switch_inputt |  | 1
~ | ToF5 | ToF_VL53L0X |  | 1
Conn_01x02 | J5 | PinHeader_1x02_P2.54mm_Vertical |  | 1
1.2kΩ | R12 | R_Axial_DIN0207_L6.3mm_D2.5mm_P2.54mm_Vertical |  | 1
~ | M1 | PinHeader_Motor_Encoder |  | 1
2kΩ | R24 | R_Axial_DIN0207_L6.3mm_D2.5mm_P2.54mm_Vertical |  | 1
~ | Buzzer1 | Buzzer-Active |  | 1
2kΩ | R23 | R_Axial_DIN0207_L6.3mm_D2.5mm_P2.54mm_Vertical |  | 1
2kΩ | R16 | R_Axial_DIN0207_L6.3mm_D2.5mm_P2.54mm_Vertical |  | 1
~ | ESC2 | ESCs |  | 1
PCA9685 | J3 | PCA9685_Breakout |  | 1
1.2kΩ | R22 | R_Axial_DIN0207_L6.3mm_D2.5mm_P2.54mm_Vertical |  | 1
~ | ESC3 | ESCs |  | 1
220Ω | R3 | R_Axial_DIN0207_L6.3mm_D2.5mm_P2.54mm_Vertical |  | 1
LED_RGAB | D2 | LED_D5.0mm-4_RGB_Staggered_Pins |  | 1
Pico | U1 | RPi_Pico_SMD_TH |  | 1
1.2kΩ | R20 | R_Axial_DIN0207_L6.3mm_D2.5mm_P2.54mm_Vertical |  | 1
220Ω | R4 | R_Axial_DIN0207_L6.3mm_D2.5mm_P2.54mm_Vertical |  | 1
~ | ToF4 | ToF_VL53L0X |  | 1
2kΩ | R18 | R_Axial_DIN0207_L6.3mm_D2.5mm_P2.54mm_Vertical |  | 1
1.2kΩ | R14 | R_Axial_DIN0207_L6.3mm_D2.5mm_P2.54mm_Vertical |  | 1
2kΩ | R26 | R_Axial_DIN0207_L6.3mm_D2.5mm_P2.54mm_Vertical |  | 1
~ | StepDown5V3.2A1 | Step Down 5V 3.2A |  | 1
220Ω | R5 | R_Axial_DIN0207_L6.3mm_D2.5mm_P2.54mm_Vertical |  | 1
~ | TCA9548A1 | TCA9548A_Multiplexer_I2C |  | 1
10uF | C2 | CP_Radial_D5.0mm_P2.00mm |  | 1
~ | M3 | PinHeader_Motor_Encoder |  | 1
2kΩ | R15 | R_Axial_DIN0207_L6.3mm_D2.5mm_P2.54mm_Vertical |  | 1
~ | Power1 | Power_PinHeader_4 |  | 1
220Ω | R6 | R_Axial_DIN0207_L6.3mm_D2.5mm_P2.54mm_Vertical |  | 1
GPIO | J2 | PinSocket_2x20_P2.54mm_Vertical |  | 1

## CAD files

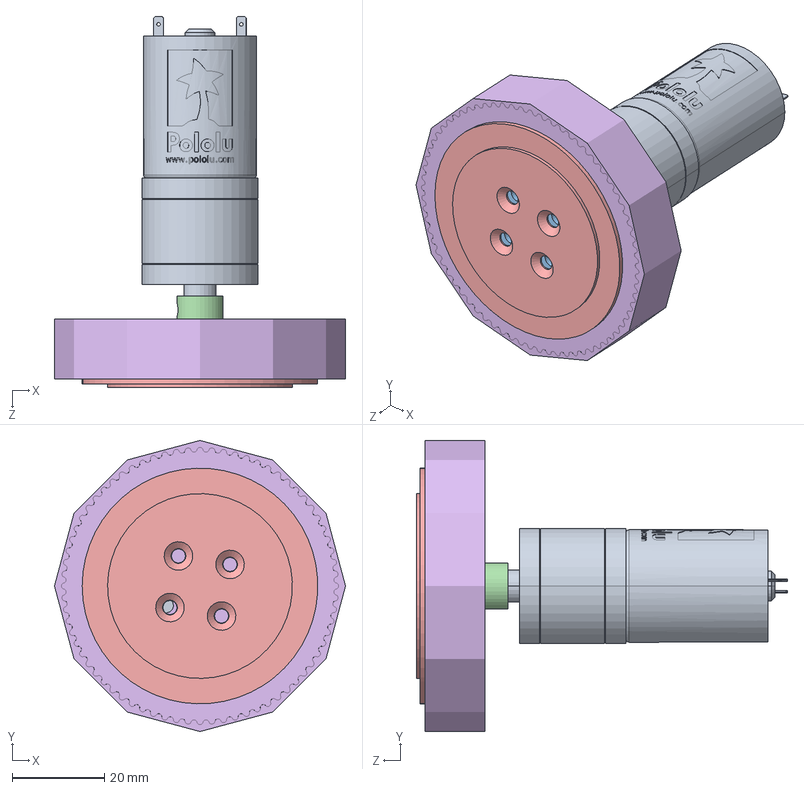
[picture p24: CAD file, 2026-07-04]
Hardware/CAD/Wheel Integration/V2/Wheel_Integration_V2.SLDASM
63.0 x 63.0 x 80.3 mm
Body_25d_Metal_Gearmotor_99to1
Shaft_25d_Metal_Gearmotor_99to1
Wheel_Rim_Inside_V2
Motor_Axle_Acopolator
Wheel_Rim_Outside_V2
Silicone_Tire

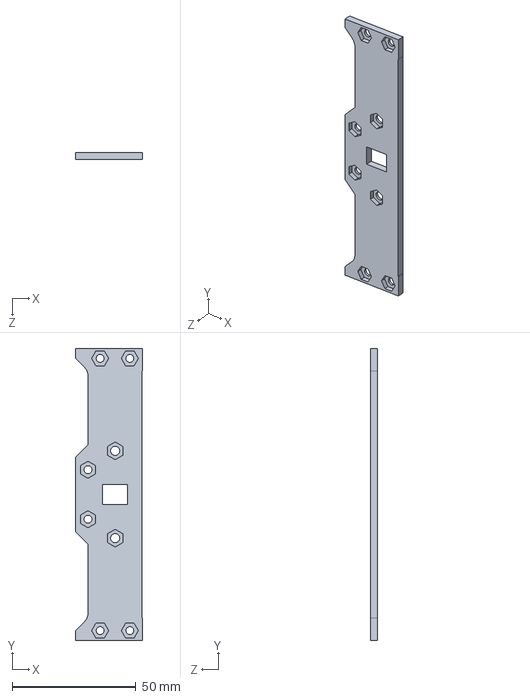
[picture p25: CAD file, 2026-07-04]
Hardware/CAD/Arm Gripper/Mid_Main_Plate.SLDPRT
27.0 x 118.0 x 3.00 mm

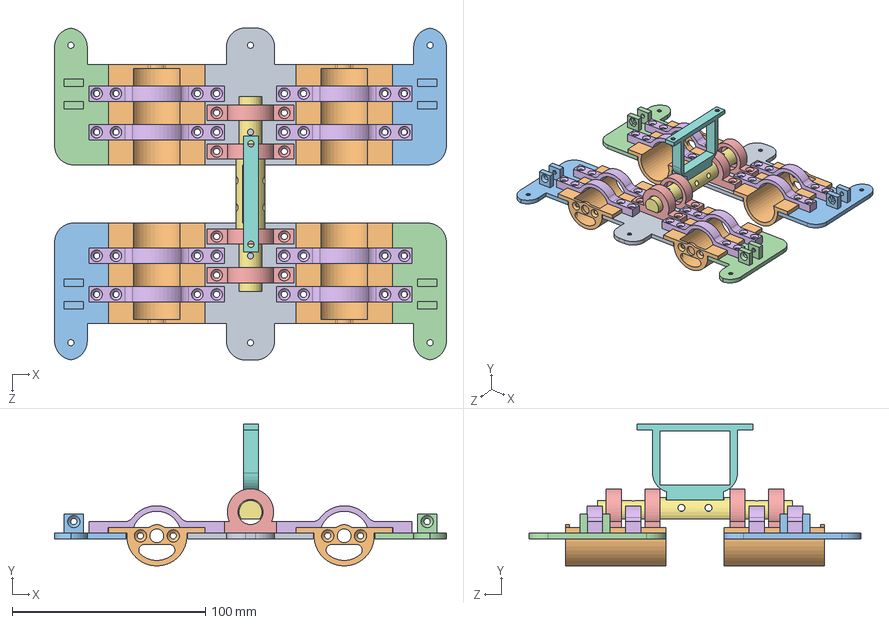
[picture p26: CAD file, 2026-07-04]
Hardware/CAD/Robot_Base/Robot_Base.SLDASM
202.9 x 73.5 x 172.0 mm
Main_Base_Plate_1 x 2
Motor_Support x 4
Suspension_Support_Base_1 x 2
Suspension_Support_Base_2 x 2
Axle_Bearing_Support x 4
Base_Joint_Extra_Support x 8
Base_Plate_Axle
Axle_to_Top_Pilar

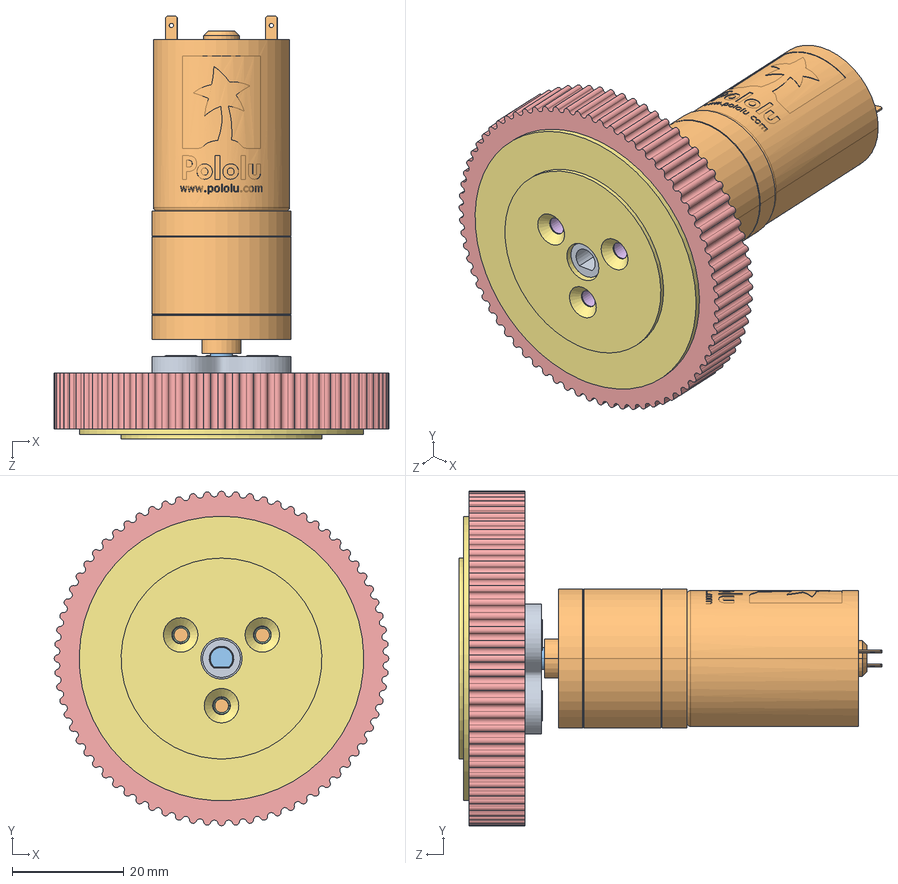
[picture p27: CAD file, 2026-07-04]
Hardware/CAD/Wheel Integration/Wheel_Integration.SLDASM
60.0 x 60.0 x 75.8 mm
Wheel_Rim_Axle
Body_25d_Metal_Gearmotor_99to1
Shaft_25d_Metal_Gearmotor_99to1
hex nut style 1_am x 3
Silicone_Tire
Wheel_Rim_Inside
Wheel_Rim_Outside

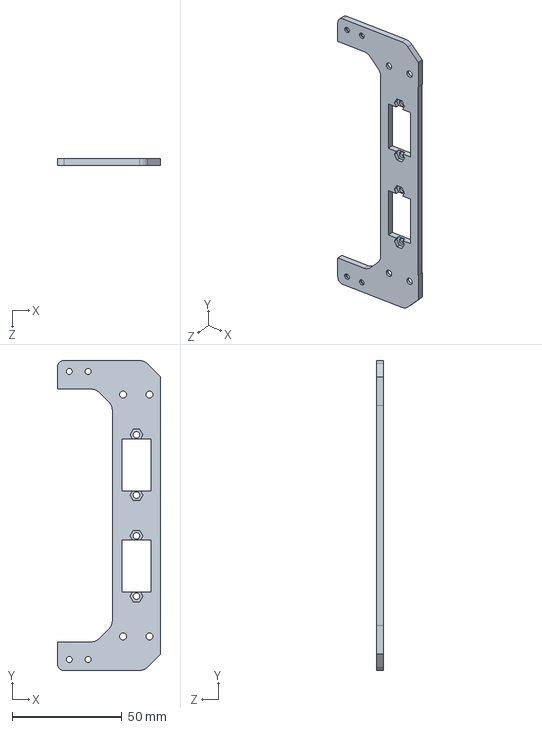
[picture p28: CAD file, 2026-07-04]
Hardware/CAD/Arm Gripper/Bottom_Main_Plate.SLDPRT
47.0 x 141.0 x 3.00 mm

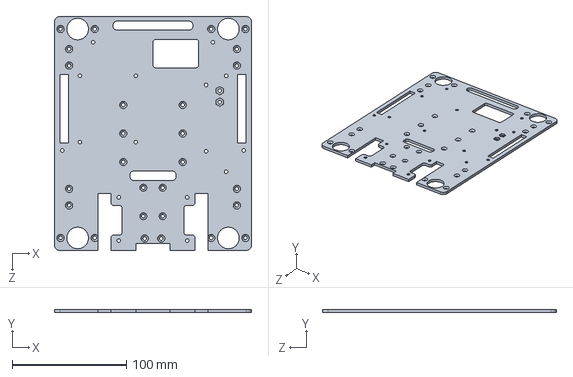
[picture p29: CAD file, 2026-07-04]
Hardware/CAD/Robot_Base/Robot_Main_Plate.SLDPRT
173.0 x 3.00 x 205.0 mm

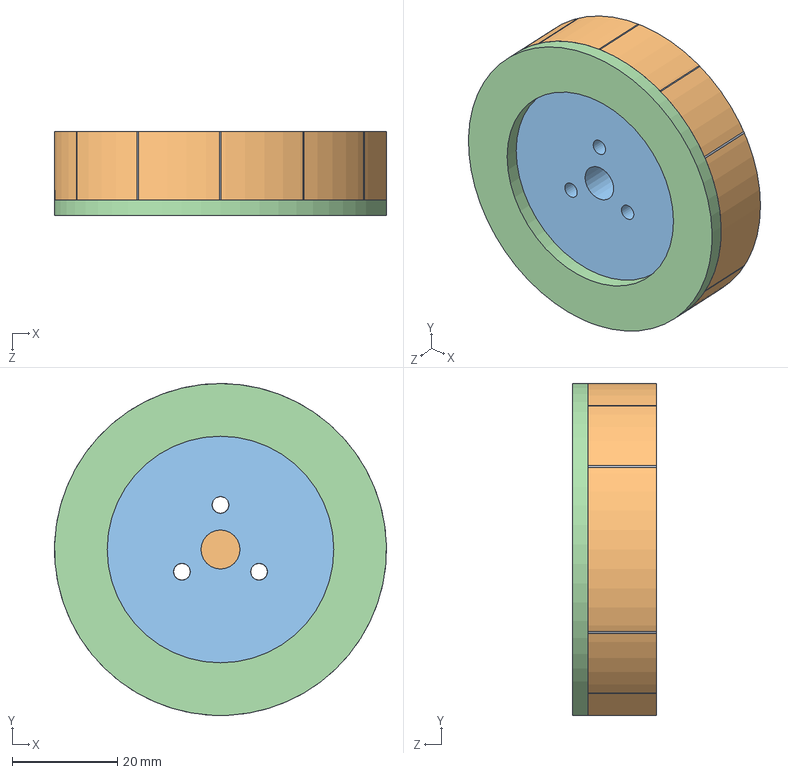
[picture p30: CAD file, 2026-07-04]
Hardware/CAD/Wheel Integration/Silicone_Tire_Mold_Setup.SLDASM
63.0 x 63.0 x 16.0 mm
Silicone_Tire
Silicone_Tire_Mold
Wheel_Rim
Silicone_Tire_Mold_Cover

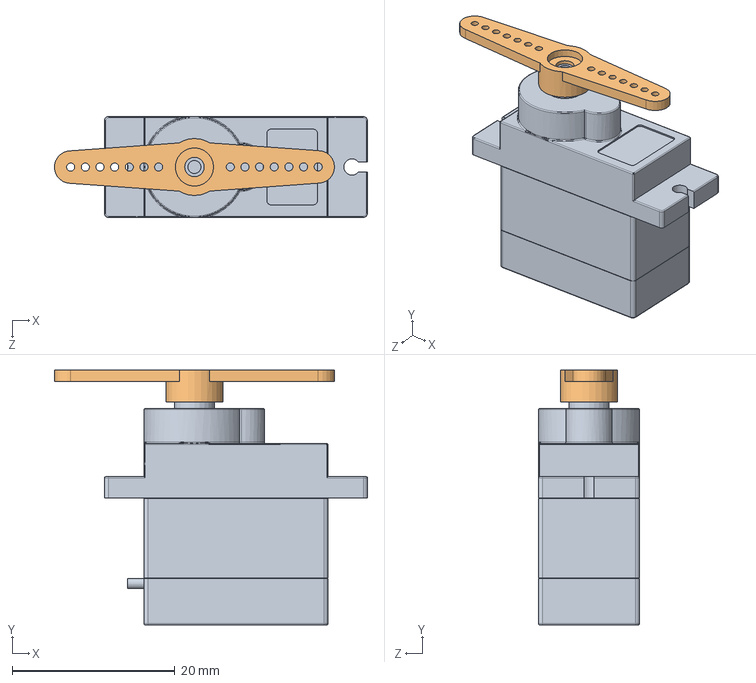
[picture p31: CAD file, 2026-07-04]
Hardware/CAD/Arm Gripper/microservoAssembly.SLDASM
38.4 x 31.3 x 12.4 mm
microservoSG90
microservoArm

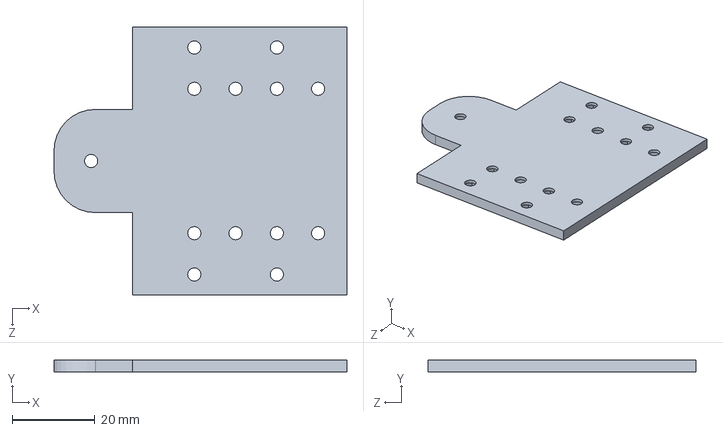
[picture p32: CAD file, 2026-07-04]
Hardware/CAD/Robot_Base/Main_Base_Plate_1.SLDPRT
71.0 x 3.00 x 65.0 mm

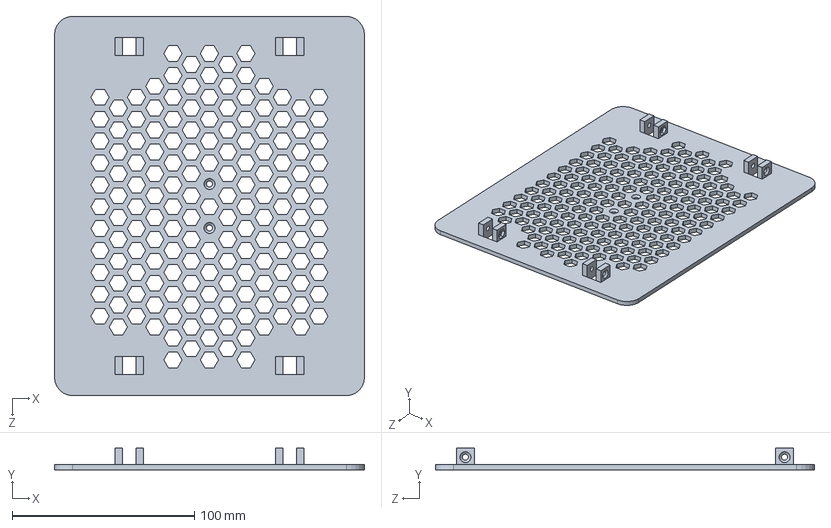
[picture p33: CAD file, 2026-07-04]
Hardware/CAD/Robot_Base/Main_Top_Plate.SLDPRT
170.0 x 12.0 x 208.0 mm

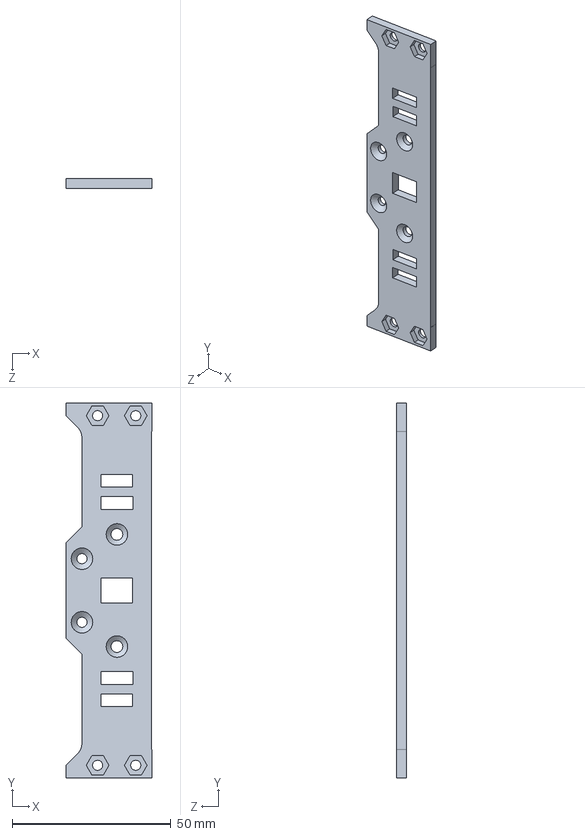
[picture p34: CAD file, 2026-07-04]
Hardware/CAD/Arm Gripper/Top_Main_Plate.SLDPRT
27.0 x 118.0 x 3.00 mm

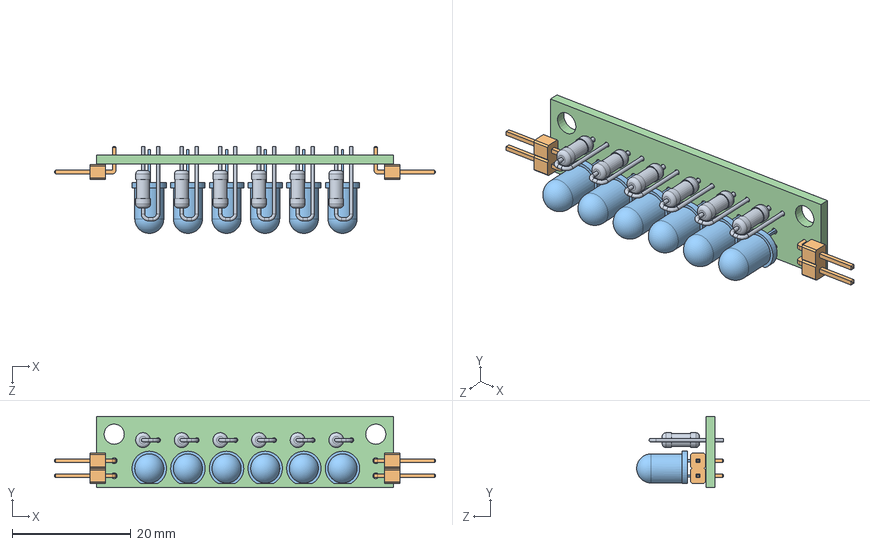
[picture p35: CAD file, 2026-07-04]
Hardware/CAD/Eletronic Components/Led_Bar_PCB.SLDASM
64.1 x 12.0 x 14.6 mm
R_Axial_DIN0207_L6.3mm_D2.5mm_P2.54mm_Vertical.step x 6
PinHeader_1x02_P2.54mm_Horizontal.step x 2
LED_D5.0mm.step x 6
Led_Bar_PCB.step

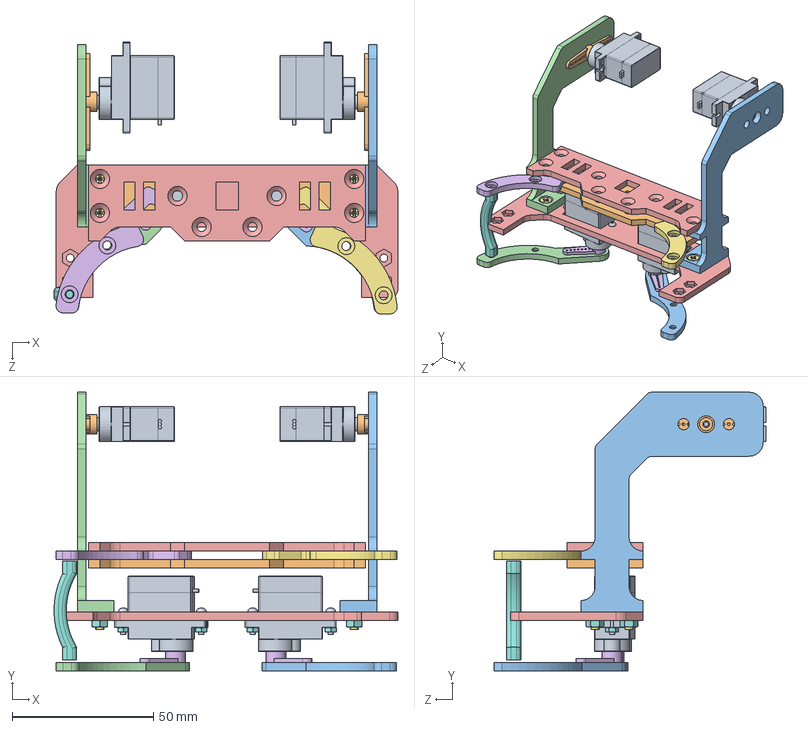
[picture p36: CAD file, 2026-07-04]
Hardware/CAD/Arm Gripper/Arm_Gripper_Integration.SLDASM
121.8 x 98.7 x 96.4 mm
microservoSG90 x 4
microservoArm x 2
Left_Servo_Attachment_Arm_Gripper
Right_Servo_Attachment_Arm_Gripper
Bottom_Main_Plate
Microservo_2_Sided_Arm_V2 x 2
flat head screw_am x 4
hex nut style 1_am x 8
M2x8mm_Screw_head x 4
Mid_Main_Plate
Right_Bottom_Hand
Left_Bottom_Hand
Top_Main_Plate
Right_Top_Hand
Left_Top_hand
Hand_Support_Pin

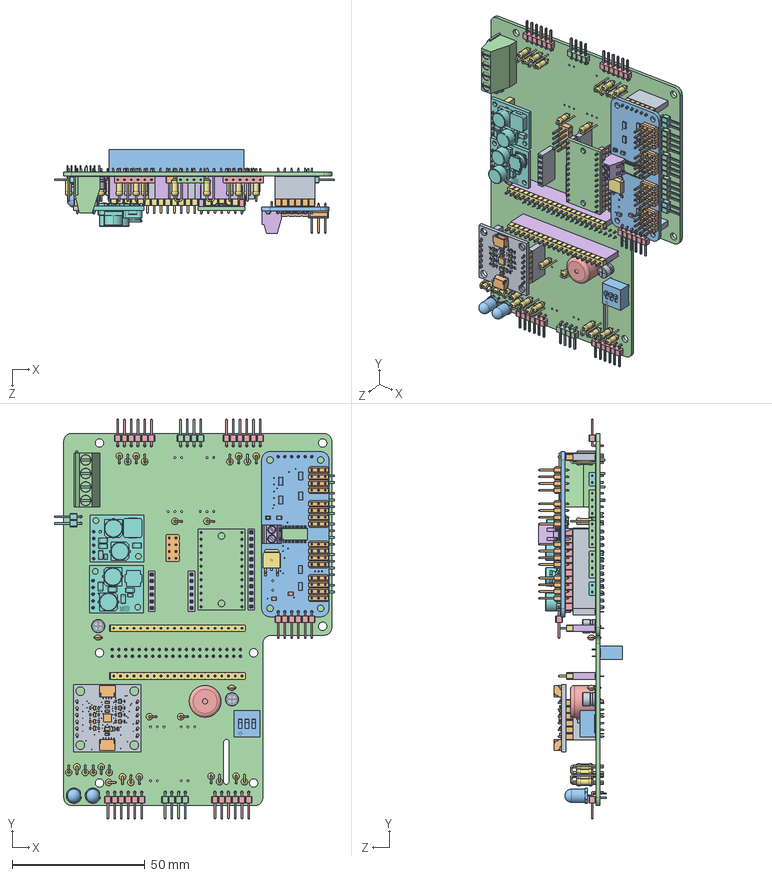
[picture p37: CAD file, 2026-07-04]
Hardware/CAD/Eletronic Components/Airborne_Main_PCB_V2.SLDASM
105.6 x 150.6 x 31.8 mm
=_[0_1_1_2].step
=_[0_1_1_81].step
Board.step
TSSOP28.step
0805-NO.step x 2
TERMBLOCK_1X2-3.5MM.step
TO252.step
CHIPLED_0805_NOOUTLINE.step
_0805MP.step
3X04.step x 4
RESPACK_4X0603.step x 6
Main_PCB 1.67.1.step
Main_PCB 1.67.2.step
Main_PCB 1.67.3.step
Main_PCB 1.67.4.step
Main_PCB 1.67.5.step
Main_PCB 1.67.6.step
Main_PCB 1.67.7.step
Main_PCB 1.67.8.step
Main_PCB 1.67.9.step
Main_PCB 1.67.10.step
Main_PCB 1.67.11.step
R_Axial_DIN0207_L6.3mm_D2.5mm_P2.54mm_Vertical.step x 26
PinHeader_1x02_P2.54mm_Horizontal.step x 3
PinSocket_1x06_P2.54mm_Vertical.step x 6
PinHeader_1x06_P2.54mm_Vertical.step x 3
LED_D5.0mm-4_RGB_Staggered_Pins.step x 2
PinHeader_1x04_P2.54mm_Horizontal.step x 5
PinHeader_1x06_P2.54mm_Horizontal.step x 5
PinHeader_1x05_P2.54mm_Vertical.step x 2
PinSocket_1x05_P2.54mm_Vertical.step x 2
d24v50f5-step-down-voltage-regulator.step
CP_Radial_D5.0mm_P2.00mm.step x 2
C_Disc_D3.0mm_W2.0mm_P2.50mm.step x 2
SW_DIP_SPSTx03_Slide_9.78x9.8mm_W7.62mm_P2.54mm.step
TerminalBlock_Phoenix_MKDS-1,5-4-5.08_1x04_P5.08mm_Horizontal.step
Buzzer_12x9.5RM7.6.step
PinSocket_1x20_P2.54mm_Vertical.step x 2
PinHeader_1x20_P2.54mm_Vertical.step x 2
d36v28fx-step-down-voltage-regulators(1).step
PinSocket_1x12_P2.54mm_Vertical.step x 2
PinHeader_2x04_P2.54mm_Vertical.step
PinSocket_2x20_P2.54mm_Vertical.step
Main_PCB_PCB.step

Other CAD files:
Hardware/CAD/Eletronic Components/SLOT_CARD_ASM.STEP.SLDASM
Hardware/CAD/Robot_Base/Main_Switch_Mount.SLDPRT
Hardware/CAD/Eletronic Components/RASPBERRY_PI_5.STEP.SLDASM
Hardware/CAD/Eletronic Components/Main_PCB.SLDASM
Hardware/CAD/Arm Gripper/Hand_Support_Pin.SLDPRT
Hardware/CAD/Arm Gripper/Left_Bottom_Hand.SLDPRT
Hardware/CAD/Arm Gripper/Left_Servo_Attachment_Arm_Gripper.SLDPRT
Hardware/CAD/Arm Gripper/Left_Top_hand.SLDPRT
Hardware/CAD/Arm Gripper/M2_Nut.SLDPRT
Hardware/CAD/Arm Gripper/M2x8mm_Screw_head.SLDPRT
Hardware/CAD/Arm Gripper/M3_Nut.SLDPRT
Hardware/CAD/Arm Gripper/M3x10mm_Countersunk.SLDPRT
Hardware/CAD/Arm Gripper/Microservo_2_Sided_Arm.SLDPRT
Hardware/CAD/Arm Gripper/Microservo_2_Sided_Arm_V2.SLDPRT
Hardware/CAD/Arm Gripper/Right_Bottom_Hand.SLDPRT
Hardware/CAD/Arm Gripper/Right_Servo_Attachment_Arm_Gripper.SLDPRT
Hardware/CAD/Arm Gripper/Right_Top_Hand.SLDPRT
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

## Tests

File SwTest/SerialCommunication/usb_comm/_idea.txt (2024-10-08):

--- New application here, help debug the serial comms:

Save in one array various critical times, and then plot them to see what happened

--- Original idea, for "Paredes de Coura":

FPG Airborne line follow R-Pi-Pico:
- main params (blackThreshold, normalSpeed, KP, KD, KI, ...)
- save in a circular array (struct or class?): time, sensors, nBlack, err, motor speeds
- calc new state (state change) based on flags (wallNear, laneLostTime, ...)
- switch on loopMode

- loopMode:  m0_Stop, m1_Calib, m2_LineFollow, m3_GoBackToLine, m4_WithinWalls, m5_ExploreToFindLine...
- globalFlags / active functions:  detectColorsFlag, beepOnColorFlag, waitOnColorFlag, ...
- private vars: workingLevel (only setWorkingLevel(n) can change it)

- log sensor readings all along the path

Raspberry Pi3:
- dataLogger, work all the time (restart upon crash?) but change filename upon a large pause on data
- how to get flags into the pi pico? sd card would be great, but R-pi3 can use USB to send cmds.
- need to make a protocol "I say over, then you can speak, you say over, then I can speak. You start."

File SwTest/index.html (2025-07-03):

# Live Robot Data

Connect

## General Info

Timestamp:

Terminate:

Run Time:

Objective:

Avoiding Being Stuck:

Data 1:

Data 2:

Data 3:

Data 4:

Data 5:

LOP State:

LOP Override:

LOP Counter:

Motor Override:

Image Similarity:

Left Motors:

Right Motors:

Motor Difference:

Pitch:

Stuck Detected:

Accel X:

Accel Y:

Accel Z:

Ramp Detected:

Was On Ramp:

Gyro X:

Gyro Y:

Gyro Z:

Ramp Up:

Ramp Down:

ToF 1:

ToF 2:

ToF 3:

ToF 4:

ToF 5:

Data 21:

Data 22:

Data 23:

Data 24:

Data 25:

## 📏 Line Following

Line Center X:

Line Angle:

Line Angle Normalized:

Data 4:

POI Choice Reason:

Line Bias:

Angle Bias:

Data 8:

Data 9:

Line Crop Percentage:

Image Cropped:

Line Detected:

In Gap:

Red Strip Detected:

Intersection Direction:

Gap Angle:

Gap Center X

Gap Center Y:

Data 19:

Data 20:

Silver Strip Confidence:

Silver Strip Average:

Silver Line Detected:

Gap State:

Gap Direction:

Silver Line Angle:

Silver Line Center X:

Silver Line Center Y:

Data 29:

Data 30:

## 🧯 Evacuation Zone

Evacuation Zone Time:

Rescued Alive:

Rescued Dead:

Picked Up Alive:

Picked Up Dead:

Zone Status:

Data 7:

Data 8:

Picking Victim:

Data 10:

Ball Exists:

Ball Center X:

Ball Bottom Y:

Ball Width:

Ball Type:

Data 16:

Data 17:

Data 18:

Data 19:

Data 20:

Motor Override LOP Override LOP State Line Following Evacuation Zone Not Started Begin Entry Find Victims Go To Ball Deposit Green Deposit Red Exit Terminate

## 🖥️ Console

Send

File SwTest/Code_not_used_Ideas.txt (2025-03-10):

- Create White Rectangular Corners:

# Set top-left and top-right corners to white (255)
# You can adjust the size of the ignored corners by changing the size of the slice
corner_size = int(width * 0.2)  # Adjust percentage as needed
blackImage[:corner_size, :corner_size] = 0 #255  # Top-left corner
blackImage[:corner_size, -corner_size:] = 0 #255  # Top-right corner

- Black image Processing with normalization by white mask:

normalized_img = (cv2_img / white_gray[:, :, None]) * np.mean(white_gray)
normalized_img = np.clip(normalized_img, 0, 255).astype(np.uint8) 
            
grayImage = cv2.cvtColor(normalized_img, cv2.COLOR_BGR2GRAY) # Convert to grayscale for black region detection  
            
blackImage = cv2.inRange(grayImage, black_min, black_max) # Apply thresholding to detect black areas

- First version of black detection

#blackImage = cv2.inRange(hsvImage, black_min, black_max)

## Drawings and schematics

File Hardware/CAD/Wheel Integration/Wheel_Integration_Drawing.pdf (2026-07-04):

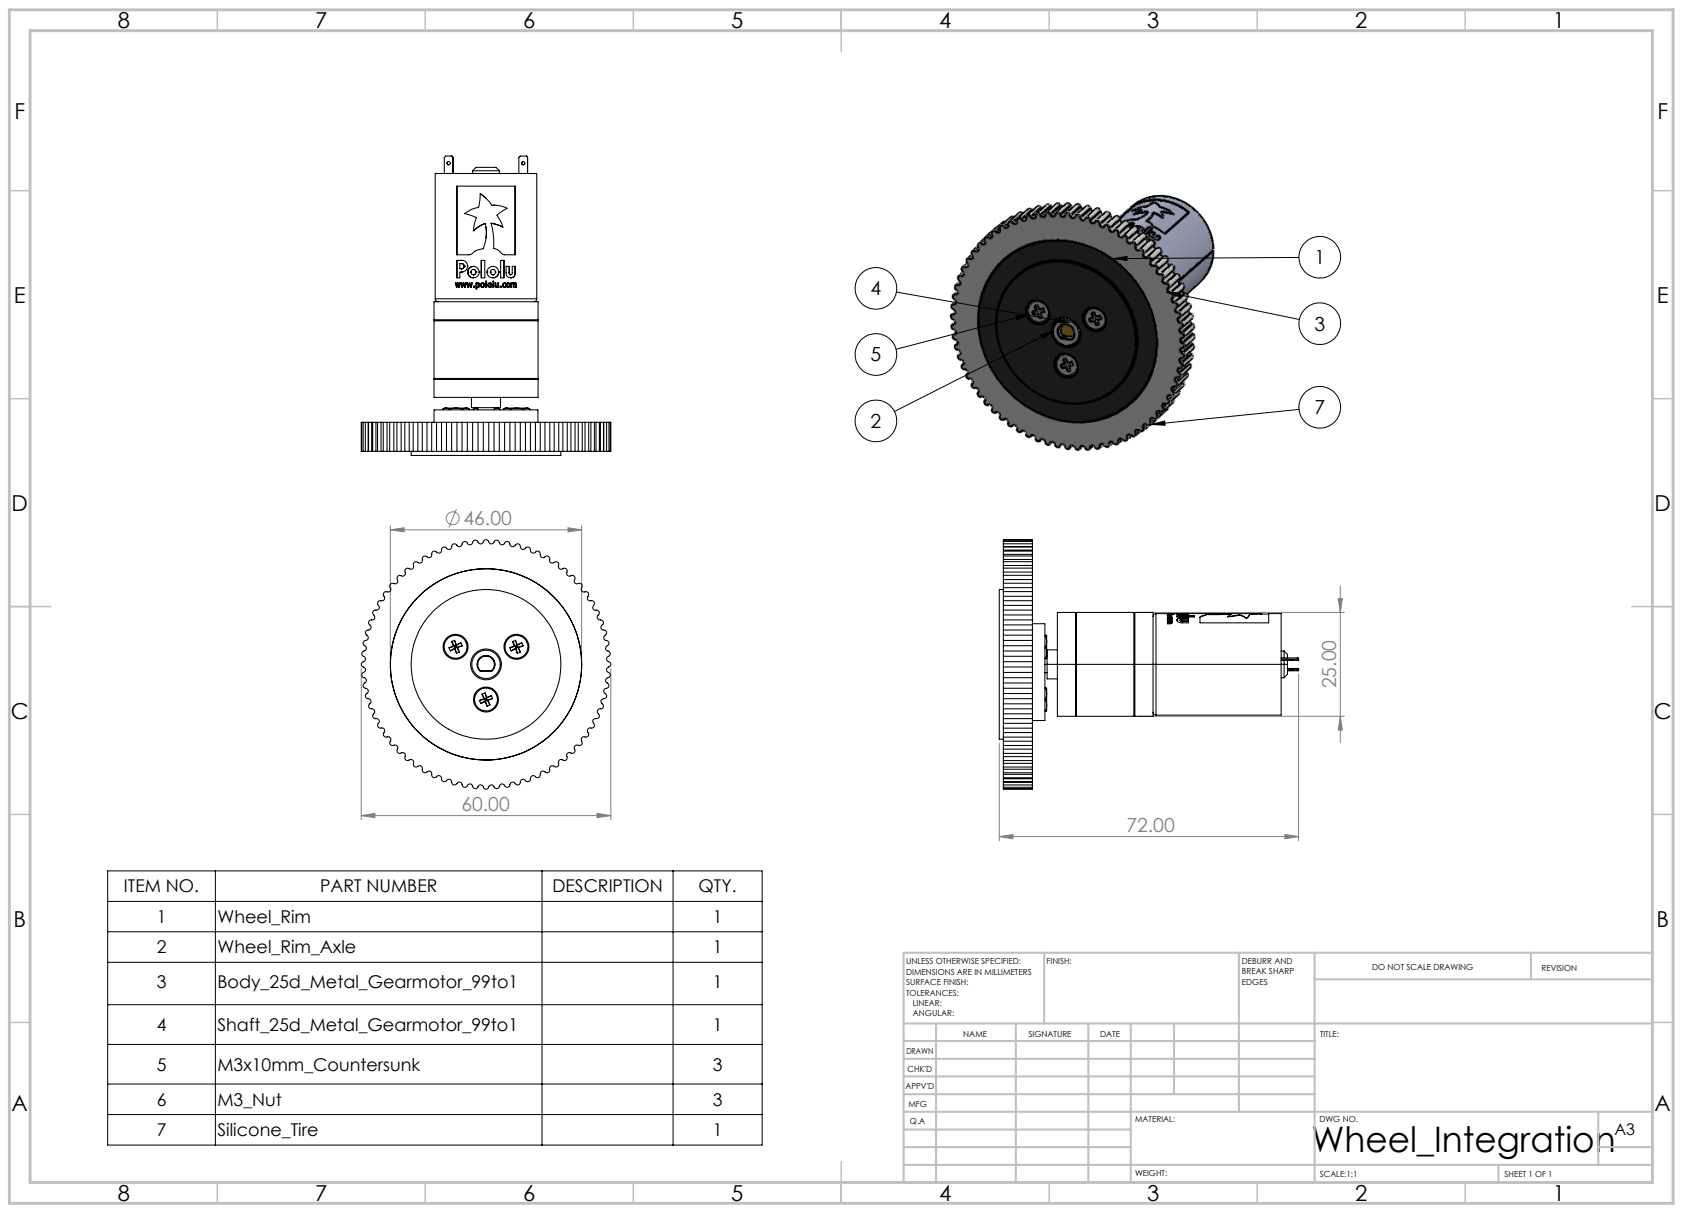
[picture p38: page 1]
FINISH:; DEBURR AND; BREAK SHARP; DO NOT SCALE DRAWING; REVISION; DWG NO.; SCALE:1:1; SHEET 1 OF 1

ITEM NO. | PART NUMBER | DESCRIPTION | QTY.
1 | Wheel_Rim | | 1
2 | Wheel_Rim_Axle | | 1
3 | Body_25d_Metal_Gearmotor_99to1 | | 1
4 | Shaft_25d_Metal_Gearmotor_99to1 | | 1

UNLESS OTHERWISE SPECIFIED:
DIMENSIONS ARE IN MILLIMETERS
SURFACE FINISH:
TOLERANCES:
LINEAR:
ANGULAR:

NAME | SIGNATURE | DATE | TITLE:

CHK'D
APPV'D
MFG

6 | M3_Nut | 3

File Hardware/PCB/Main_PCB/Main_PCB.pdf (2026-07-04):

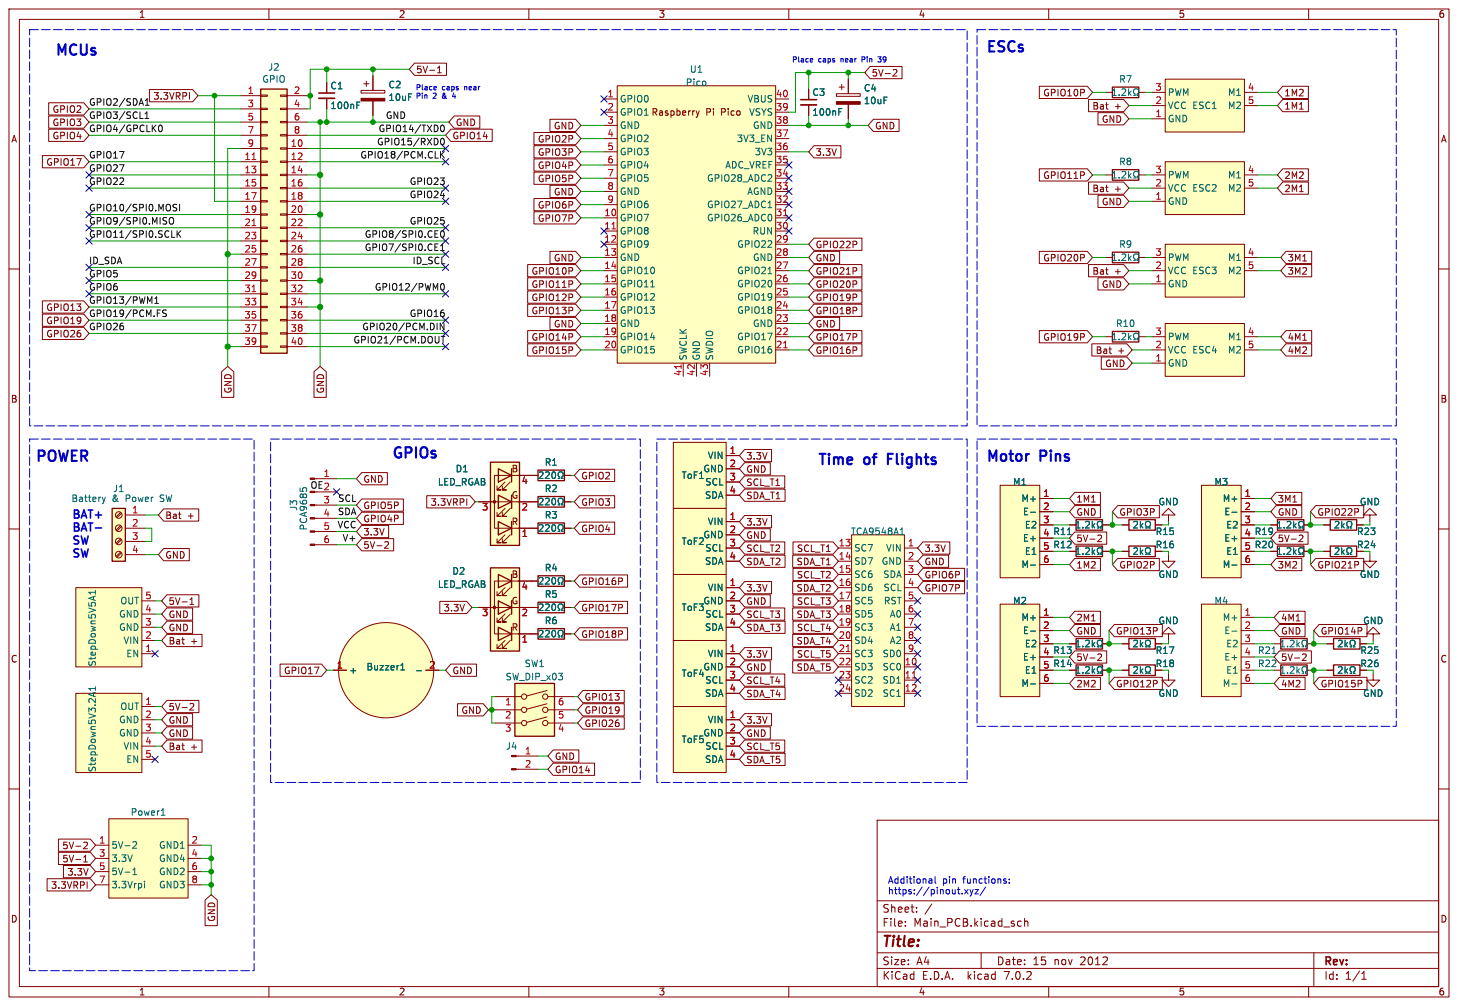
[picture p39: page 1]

ID_SCL GPIO20/PCM.DIN GPIO21/PCM.DOUT GPIO16 GPIO12/PWM0 V+ VCC

R26 þÿ2k©GND GND GND

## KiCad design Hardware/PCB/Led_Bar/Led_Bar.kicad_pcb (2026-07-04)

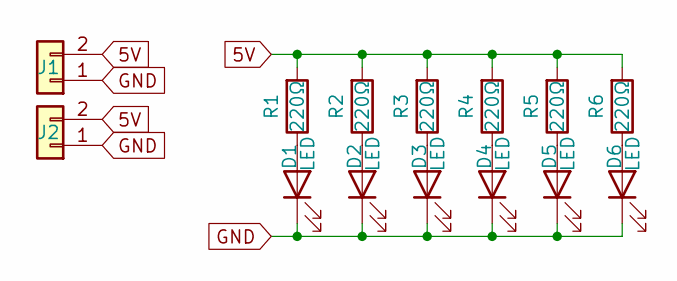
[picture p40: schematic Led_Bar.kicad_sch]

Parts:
D1, D2, D3, D4, D5, D6: LED; LED_D5.0mm
J1, J2: Conn_01x02; PinHeader_1x02_P2.54mm_Vertical
R1, R2, R3, R4, R5, R6: 220Ω; R_Axial_DIN0207_L6.3mm_D2.5mm_P2.54mm_Vertical

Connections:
5V: J1.2, J2.2, R1.2, R2.2, R3.2, R4.2, R5.2, R6.2
GND: D1.1 (K), D2.1 (K), D3.1 (K), D4.1 (K), D5.1 (K), D6.1 (K), J1.1, J2.1
unnamed: D1.2 (A), R1.1
unnamed: D2.2 (A), R2.1
unnamed: D3.2 (A), R3.1
unnamed: D4.2 (A), R4.1
unnamed: D5.2 (A), R5.1
unnamed: D6.2 (A), R6.1

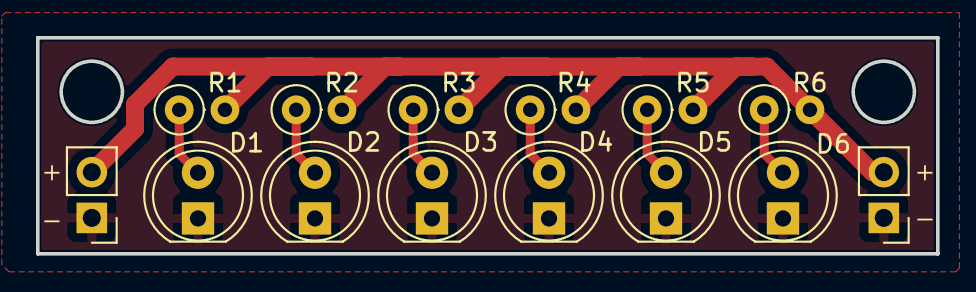
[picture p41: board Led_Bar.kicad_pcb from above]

Board: 2 copper layers, 50.0 x 12.0 mm, 14 parts (0 on the bottom side), 8 nets.

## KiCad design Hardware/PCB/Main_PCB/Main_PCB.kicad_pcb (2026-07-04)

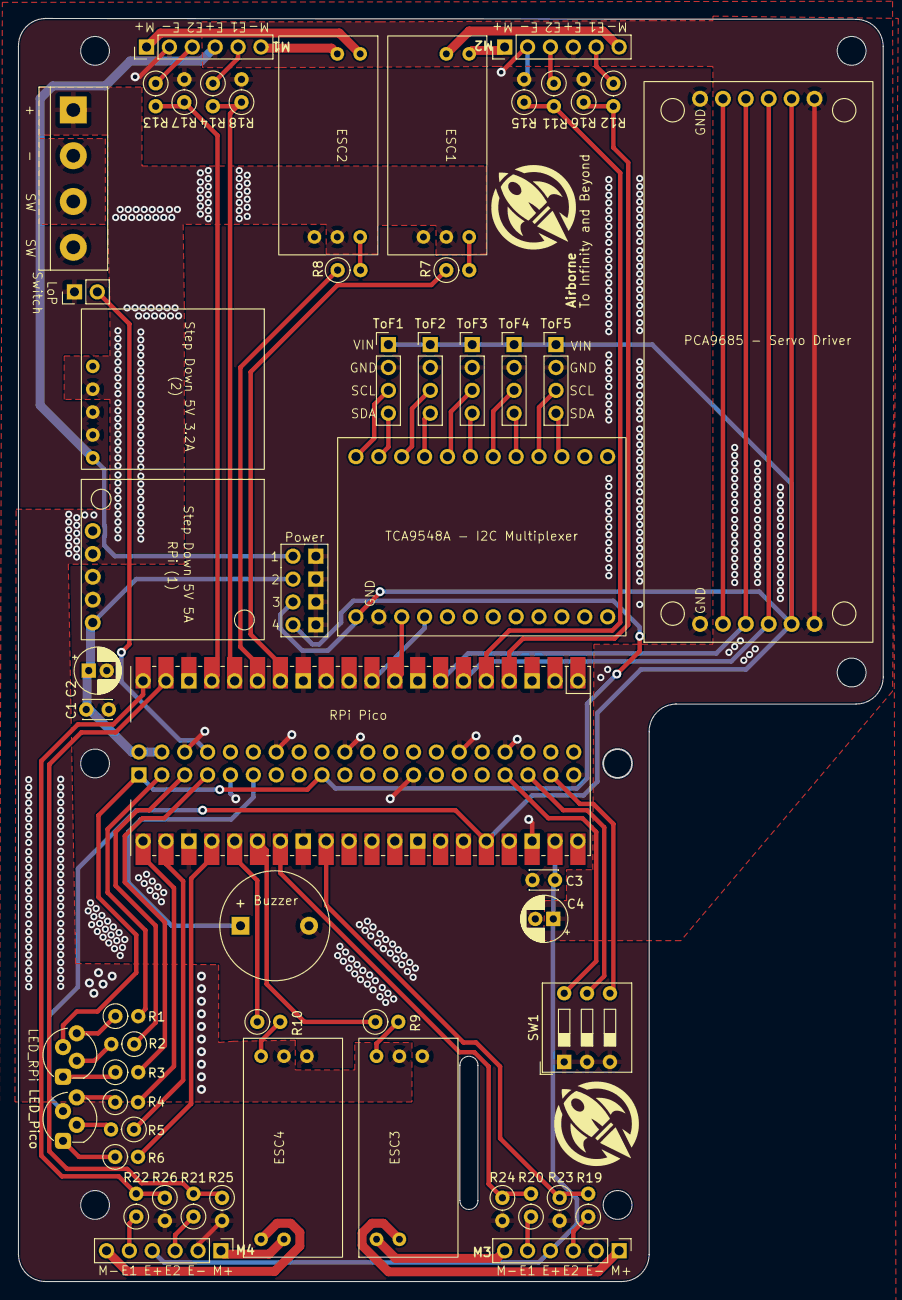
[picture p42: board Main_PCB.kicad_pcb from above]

Board: 2 copper layers, 96.0 x 140.2 mm, 61 parts (1 on the bottom side), 70 nets.

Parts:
Buzzer1: Buzzer-Active
C1, C3: 100nF; C_Disc_D3.0mm_W2.0mm_P2.50mm
C2, C4: 10uF; CP_Radial_D5.0mm_P2.00mm
ESC1, ESC2, ESC3, ESC4: ESCs
J1: Battery & Power SW; Power_Switch_inputt
J3: PCA9685; PCA9685_Breakout
J4: Conn_01x02_Pin; PinHeader_1x02_P2.54mm_Vertical
LED_Pico: LED_RGAB; LED_D5.0mm-4_RGB_Staggered_Pins
LED_RPi: LED_RGAB; LED_D5.0mm-4_RGB_Staggered_Pins
M1, M2, M3, M4: PinHeader_Motor_Encoder
MH1, MH3, MH4, MH4#2, MH4#3: MountingHole_2.7mm_M2.5
Power1: Power_PinHeader_4
R1, R2, R3, R4, R5, R6: 220Ω; R_Axial_DIN0207_L6.3mm_D2.5mm_P2.54mm_Vertical
R7, R8, R9, R10, R11, R12, R13, R14, R19, R20, R21, R22: 1.2kΩ; R_Axial_DIN0207_L6.3mm_D2.5mm_P2.54mm_Vertical
R15, R16, R17, R18, R23, R24, R25, R26: 2kΩ; R_Axial_DIN0207_L6.3mm_D2.5mm_P2.54mm_Vertical
RPi Pico: Pico; RPi_Pico_SMD_TH
Raspberry Pi 5: GPIO; PinSocket_2x20_P2.54mm_Vertical
SW1: SW_DIP_x03; SW_DIP_SPSTx03_Slide_9.78x9.8mm_W7.62mm_P2.54mm
StepDown5V3.2A1: Step Down 5V 3.2A
StepDown5V5A1: Step_Down_5V_5A_D24V50F5
TCA9548A1: TCA9548A_Multiplexer_I2C
ToF1, ToF2, ToF3, ToF4, ToF5: ToF_VL53L0X

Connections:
1M1: ESC1.5 (M2), M1.1 (M+)
1M2: ESC1.4 (M1), M1.6 (M-)
2M1: ESC2.5 (M2), M2.1 (M+)
2M2: ESC2.4 (M1), M2.6 (M-)
3.3V: J3.5, LED_Pico.3 (A), Power1.5 (5V-1), RPi Pico.36 (3V3), TCA9548A1.1 (VIN), ToF1.1 (VIN), ToF2.1 (VIN), ToF3.1 (VIN), ToF4.1 (VIN), ToF5.1 (VIN)
3.3VRPI: LED_RPi.3 (A), Power1.7 (3.3Vrpi), Raspberry Pi 5.1, Raspberry Pi 5.17
3M1: ESC3.4 (M1), M3.1 (M+)
3M2: ESC3.5 (M2), M3.6 (M-)
4M1: ESC4.4 (M1), M4.1 (M+)
4M2: ESC4.5 (M2), M4.6 (M-)
5V-1: C1.1, C2.1, Power1.3 (3.3V), Raspberry Pi 5.2, Raspberry Pi 5.4, StepDown5V5A1.5 (OUT)
5V-2: C3.1, C4.1, J3.6, M1.4 (E+), M2.4 (E+), M3.4 (E+), M4.4 (E+), Power1.1 (5V-2), RPi Pico.39 (VSYS), StepDown5V3.2A1.1 (OUT)
Bat +: ESC1.2 (VCC), ESC2.2 (VCC), ESC3.2 (VCC), ESC4.2 (VCC), J1.1, StepDown5V3.2A1.4 (VIN), StepDown5V5A1.2 (VIN)
GND: Buzzer1.2 (-), C1.2, C2.2, C3.2, C4.2, ESC1.1 (GND), ESC2.1 (GND), ESC3.1 (GND), ESC4.1 (GND), J1.4, J3.1, J4.1, M1.2 (E-), M2.2 (E-), M3.2 (E-), M4.2 (E-), Power1.2 (GND1), Power1.4 (GND4), Power1.6 (GND2), Power1.8 (GND3), R15.2, R16.2, R17.2, R18.2, R23.2, R24.2, R25.2, R26.2, RPi Pico.3 (GND), RPi Pico.8 (GND), RPi Pico.13 (GND), RPi Pico.18 (GND), RPi Pico.23 (GND), RPi Pico.28 (GND), RPi Pico.38 (GND), Raspberry Pi 5.6, Raspberry Pi 5.9, Raspberry Pi 5.14, Raspberry Pi 5.20, Raspberry Pi 5.25, Raspberry Pi 5.30, Raspberry Pi 5.34, Raspberry Pi 5.39, SW1.1, SW1.2, SW1.3, StepDown5V3.2A1.2 (GND), StepDown5V3.2A1.3 (GND), StepDown5V5A1.3 (GND), StepDown5V5A1.4 (GND), TCA9548A1.2 (GND), ToF1.2 (GND), ToF2.2 (GND), ToF3.2 (GND), ToF4.2 (GND), ToF5.2 (GND)
GPIO2: R1.2, Raspberry Pi 5.3
GPIO2P: R12.2, R16.1, RPi Pico.4 (GPIO2)
GPIO3: R2.1, Raspberry Pi 5.5
GPIO3P: R11.2, R15.1, RPi Pico.5 (GPIO3)
GPIO4: R3.2, Raspberry Pi 5.7
GPIO4P: J3.4, RPi Pico.6 (GPIO4)
GPIO5P: J3.3, RPi Pico.7 (GPIO5)
GPIO6P: RPi Pico.9 (GPIO6), TCA9548A1.3 (SDA)
GPIO7P: RPi Pico.10 (GPIO7), TCA9548A1.4 (SCL)
GPIO10P: R7.1, RPi Pico.14 (GPIO10)
GPIO11P: R8.1, RPi Pico.15 (GPIO11)
GPIO12P: R14.2, R18.1, RPi Pico.16 (GPIO12)
GPIO13: Raspberry Pi 5.33, SW1.6
GPIO13P: R13.2, R17.1, RPi Pico.17 (GPIO13)
GPIO14: J4.2, Raspberry Pi 5.8
GPIO14P: R21.2, R25.1, RPi Pico.19 (GPIO14)
GPIO15P: R22.2, R26.1, RPi Pico.20 (GPIO15)
GPIO16P: R4.2, RPi Pico.21 (GPIO16)
GPIO17: Buzzer1.1 (+), Raspberry Pi 5.11
GPIO17P: R5.1, RPi Pico.22 (GPIO17)
GPIO18P: R6.2, RPi Pico.24 (GPIO18)
GPIO19: Raspberry Pi 5.35, SW1.5
GPIO19P: R10.1, RPi Pico.25 (GPIO19)
GPIO20P: R9.1, RPi Pico.26 (GPIO20)
GPIO21P: R20.2, R24.1, RPi Pico.27 (GPIO21)
GPIO22P: R19.2, R23.1, RPi Pico.29 (GPIO22)
GPIO26: Raspberry Pi 5.37, SW1.4
unnamed: LED_RPi.4 (BK), R1.1
unnamed: LED_RPi.2 (GK), R2.2
unnamed: LED_RPi.1 (RK), R3.1
unnamed: LED_Pico.4 (BK), R4.1
unnamed: LED_Pico.2 (GK), R5.2
unnamed: LED_Pico.1 (RK), R6.1
unnamed: ESC1.3 (PWM), R7.2
unnamed: ESC2.3 (PWM), R8.2
unnamed: ESC3.3 (PWM), R9.2
unnamed: ESC4.3 (PWM), R10.2
unnamed: J1.2, J1.3
unnamed: M1.5 (E1), R12.1
unnamed: M1.3 (E2), R11.1
unnamed: M2.5 (E1), R14.1
unnamed: M2.3 (E2), R13.1
unnamed: M3.5 (E1), R20.1
unnamed: M3.3 (E2), R19.1
unnamed: M4.5 (E1), R22.1
unnamed: M4.3 (E2), R21.1
SCL_T1: TCA9548A1.13 (SC7), ToF1.3 (SCL)
SCL_T2: TCA9548A1.15 (SC6), ToF2.3 (SCL)
SCL_T3: TCA9548A1.17 (SC5), ToF3.3 (SCL)
SCL_T4: TCA9548A1.19 (SC3), ToF4.3 (SCL)
SCL_T5: TCA9548A1.21 (SC3), ToF5.3 (SCL)
SDA_T1: TCA9548A1.14 (SD7), ToF1.4 (SDA)
SDA_T2: TCA9548A1.16 (SD6), ToF2.4 (SDA)
SDA_T3: TCA9548A1.18 (SD5), ToF3.4 (SDA)
SDA_T4: TCA9548A1.20 (SD4), ToF4.4 (SDA)
SDA_T5: TCA9548A1.22 (SD3), ToF5.4 (SDA)

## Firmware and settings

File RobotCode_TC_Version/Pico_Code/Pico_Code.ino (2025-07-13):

#include <Servo.h>
#include <Wire.h>
#include <VL53L0X.h>
#include <Adafruit_PWMServoDriver.h>
#include "myServo.h"
#include "Motor.h"
#include "ArmGrip.h"
#include "IMU.h"
#include "ToF.h"

#include "pico/multicore.h"  // Use of second core


// --------------------------- Motor Vars ---------------------------

const int enc1A = 2;
const int enc1B = 3;
const int enc2A = 12;
const int enc2B = 13;
const int enc3A = 1;
const int enc3B = 0;
const int enc4A = 14;
const int enc4B = 15;

Motor motors[4] = {
    Motor(10, enc1A, enc1B),
    Motor(11, enc2A, enc2B),
    Motor(22, enc3A, enc3B),
    Motor(19, enc4A, enc4B)
};

int value;
int startMotorSpeed = 1520; // Default speed for just launched code
int values[4] = {startMotorSpeed,startMotorSpeed,startMotorSpeed,startMotorSpeed};


// --------------------------- Arm Vars ---------------------------

const int leftHandServo = 0; // Channel 0 for the left hand servo
const int rightHandServo = 1; // Channel 1 for the right hand servo
const int leftArmServo = 2; // Channel 2 for the left arm servo
const int rightArmServo = 3; // Channel 3 for the right arm servo

// Create the PCA9685 object
Adafruit_PWMServoDriver pwm = Adafruit_PWMServoDriver();

// Create the ArmGrip object with specified channels for servos
ArmGrip Grip(pwm, rightHandServo, leftHandServo, rightArmServo, leftArmServo);


// ----------------------- Other Servo Vars -----------------------
const int camServoChannel = 4; // Channel 4 for the Camera Tilt Servo
const int ballStorageServoChannel = 5; // Channel 5 for the Ball Storage Servo

myServo camServo(camServoChannel, pwm, true, false);
myServo ballStorageServo(ballStorageServoChannel, pwm, false, true);


// --------------------------- IMU Vars ---------------------------
IMU myIMU;


// --------------------------- TOF Vars ---------------------------
ToF myToFs(3, 4, 5, 6, 7);  // Setup sensors by mux channels
unsigned long tofT0;  // control sampling rate (period ini)
unsigned long tofT1;  // control sampling rate (period end)
long tofMeasurementSensorInterval = 50;  // 50ms in between sensors measurements (4Hz) 
int currentToFSensor = 0;



// --------------------------- LED Vars ---------------------------
const int redLed = 18;
const int greenLed = 17;
const int blueLed = 16;
const int robotLight = 8;

unsigned long ledT0;  // control sampling rate (period ini)
unsigned long ledT1;  // control sampling rate (period end)
long ledTimeInterval = 1000;  // 1s blinks

bool ledState = true;


// --------------------------- Time Vars ---------------------------
unsigned long t0;  // control sampling rate (period ini)
unsigned long t1;  // control sampling rate (period end)
long timeInterval = 2.0;  // 2.5ms per loop = 400Hz


// ----------------------------------------------------------------
// -----------------  <<<<<<<<  Setup  >>>>>>>>  ------------------
// --------------------------- ----- ------------------------------

void setup() {
  // put your setup code here, to run once:
  Serial.begin(115200);

  /*// Get Motors Ready
  for (int i = 0; i < 4; i++) {
    motors[i].getReady();
  }*/

  // I2C Communitations
  Wire.begin(); // Bus 0 GPIO 4 and 5
  Wire1.setSDA(6); 
  Wire1.setSCL(7);
  Wire1.begin(); // Bus 1 GPIO 6 and 7


  // Get The Servos Ready - Correct Position
  Grip.begin();
  Grip.defaultPosition(); // Get the Grip to its default/storage Position
  camServo.lineFollowing(); // Get the Camera to point down for line following
  ballStorageServo.close(); // Close Ball Storage

  // Let the Servos Stay Free - Avoid Shaking
  delay(1000);
  Grip.freeAllServos();
  camServo.freeServo();
  ballStorageServo.freeServo();

  // IMU Setup
  myIMU.begin(Wire);

  // ToFs Setup
  myToFs.begin(Wire1);

  // LED
  pinMode(LED_BUILTIN, OUTPUT);
  digitalWrite(LED_BUILTIN, HIGH);
  
  pinMode(redLed, OUTPUT);
  pinMode(greenLed, OUTPUT);
  pinMode(blueLed, OUTPUT);
  setRGBColor(0,255,255);

  pinMode(robotLight, OUTPUT);
  digitalWrite(robotLight, HIGH);
  delay(1000);
  digitalWrite(robotLight, LOW);

  tofT0 = millis();
  ledT0 = millis();
  t0 = millis();
}



// ---------------------------------------------------------------
// -----------------  <<<<<<<<  Loop  >>>>>>>>  ------------------
// --------------------------- ----- -----------------------------

String message = "";
void loop() {
  t1 = t0 + timeInterval;
  tofT1 = tofT0 + tofMeasurementSensorInterval;


  // Update Sensors
  myIMU.update10DOF();
  if (millis() >= tofT1) {
    myToFs.updateSingleToF(currentToFSensor);

    // Move to next sensor
    currentToFSensor++;
    if (currentToFSensor >= 5) {
        currentToFSensor = 0;  // wrap around
    }

    tofT0 = millis();
  }


  // Read Serial Port
  message = readSerial(); 

  if (message != "") {
    Serial.print("Pico Received: ");
    Serial.println(message);
  }


  // Act According Message:
  if (message.startsWith("M(") && message.endsWith(")")) { ControlMotor(message); }  // Motor Command | M(x,x)

  else if (message == "GR") {   // Arm motors again | Get Ready
    for (int i = 0; i < 4; i++) {
      motors[i].getReady();
    }
    Serial.print("Ok\n");
  }

  else if (message == "PA") { Grip.pickAlive(1); ControlMotor("M(1520, 1520)"); Grip.pickAlive(2); Serial.print("Ok\n"); }  // Pick Alive Victim Sequence Command | Pick Alive
  else if (message == "PD") { Grip.pickDead(1); ControlMotor("M(1520, 1520)"); Grip.pickDead(2); Serial.print("Ok\n"); }  // Pick Dead Victim Sequence Command | Pick Dead

  else if (message == "CL") { camServo.lineFollowing(); Serial.print("Ok\n"); }  // Point Camera Down for Line Following Command | Camera Line
  else if (message == "CE") { camServo.EvacuationZone(); Serial.print("Ok\n"); }  // Point Camera Forward for Evactuation Zone Victim Rescue Command | Camera Evacuation

  else if (message == "DA") { ballStorageServo.dropAlive(); Serial.print("Ok\n"); }  // Drop Alive Victims Command | Drop Alive
  else if (message == "DD") { ballStorageServo.dropDead(); Serial.print("Ok\n"); }  // Drop Dead Victims Command | Drop Dead
  else if (message == "BC") { ballStorageServo.close(); Serial.print("Ok\n"); } // Close Ball Storage Command | Ball Close

  else if (message == "HO") { Grip.openHand(); Serial.print("Ok\n"); }  // Open Hand Command | Hand Open
  else if (message == "HC") { Grip.closeHand(); Serial.print("Ok\n"); }  // Close Hand Command | Hand Close
  else if (message == "HA") { Grip.moveAlive(); Serial.print("Ok\n"); }  // Move Hand to Alive Position Command | Hand Alive
  else if (message == "HD") { Grip.moveDead(); Serial.print("Ok\n"); }  // Move Hand to Dead Position Command | Hand Dead

  else if (message == "AD") { Grip.moveDown(); Serial.print("Ok\n"); }  // Move Arm Down Command (Catch Position) | Arm Down
  else if (message == "AU") { Grip.moveUp(); Serial.print("Ok\n"); }  // Move Arm Up Command (Storage Position) | Arm Up

  else if (message.startsWith("SC,")) { servoControlMessage(message); Serial.print("Ok\n"); } // Control Single Servo Command | servoControl

  else if (message.startsWith("SF,")) { servoFreeControl(message); Serial.print("Ok\n"); } //Free a servo | Servo Free

  else if (message == "IMU10") { Serial.print("I10, "); Serial.println(myIMU.getAllString()); } // Print All IMU Data | IMU 10 DOF
  else if (message == "IMUAcc") { Serial.println(myIMU.getAccelString()); } // Print IMU Acceleration Data | IMU Acceleration DOF
  else if (message == "IMUGyro") { Serial.println(myIMU.getGyroString()); } // Print IMU Gyroscope Data | IMU Gyroscope DOF
  else if (message == "IMUMag") { Serial.println(myIMU.getMagString()); } // Print IMU Magnetometer Data | IMU Magnetometer DOF
  else if (message == "IMUTemp") { Serial.println(myIMU.getTempString()); } // Print IMU Temperature Data | IMU Temperature DOF

  else if (message == "ToF5") {
    myToFs.updateToF5();
    String allData = "T5, ";
    allData += myToFs.getAllString(); 
    Serial.println(allData);
  } // Print All ToF Data | ToF 5 Sensors
  else if (message.startsWith("ToFX")) { myToFs.updateToF5(); tofControlMessage(message); } // Print Specific ToF Data | ToF X Sensor

  else if (message == "ITData") {
    String allData = "D, ";
    allData += myIMU.getAllString();     // e.g., 9 IMU values + temp
    allData += ", ";
    allData += myToFs.getAllString();    // 5 TOF values
    Serial.println(allData);             // One complete line
  }

  else if (message == "L0") { digitalWrite(robotLight, LOW); Serial.print("Ok\n"); }
  else if (message == "L1") { digitalWrite(robotLight, HIGH); Serial.print("Ok\n"); }
  else if (message.startsWith("LX")) { lightControlMessage(message); Serial.print("Ok\n"); }
  
  else if (message.startsWith("RGB,")) { handleRGBCommand(message); Serial.print("Ok\n"); }
  
  else if (message == "Alive") { Serial.println("Yes Alive"); }  // Check if Pico is still alive  | Alive


  // LED Blink
  ledBlinkController(); //Blinks LED every Time Interval (ledTimeInterval = 1s)


  while (millis() <= t1) {
    delay(0.025);
  }
  delay(0.5);
  t0 = t1;
}



// --------------------------------------------------------------
// --------------  <<<<<<<<  Functions  >>>>>>>>  ---------------
// --------------------------- ----- ----------------------------


// --------------------------------------------------------------
// Function to read the serial port
String readSerial() {
  int c;
  String str = "";

  if (Serial.available() <= 0) {
    return str;
  }

  while (1) {
    c = Serial.read();
    if (c == 0 || c == 0x0A || c == 0x0D) break;
    str = str + String(char(c));
    if (Serial.available() <= 0) {
      delay(1);
      if (Serial.available() <= 0) break;
    }
  }

  return str;
}


// --------------------------------------------------------------
// Function to control Motors | Command: ControlMotor | M(X,X)
void ControlMotor(String input) {
  // Interpret Motor Controls | Update values list with motor speeds

  input = input.substring(2, input.length() - 1);

  int commaIndex = input.indexOf(',');
  if (commaIndex != -1) {
    // Get values a and b from the string
    int a = input.substring(0, commaIndex).toInt();
    int b = input.substring(commaIndex + 1).toInt();

    // Update the list with [a, a, b, b]
    values[0] = a;
    values[1] = a;
    values[2] = b;
    values[3] = b;

  }

  // Send Motor Control
  /*Serial.print("Motors Values: ");
  for (int i = 0; i < 4; i++) {
    Serial.print(values[i]);
    if (i < 3) Serial.print(", ");
  }
  Serial.println();*/

  for (int i = 0; i < 4; i++) {
    motors[i].controlMotor(values[i]);
  }

}


// --------------------------------------------------------------
// Function to Handle RGB Command | Command: RGB,X,X,X
void handleRGBCommand(String command) {
  if (command.startsWith("RGB,")) {
    int firstComma = command.indexOf(',');              // Position of first comma
    int secondComma = command.indexOf(',', firstComma + 1);
    int thirdComma = command.indexOf(',', secondComma + 1);

    if (firstComma > 0 && secondComma > firstComma && thirdComma > secondComma) {
      int red   = command.substring(firstComma + 1, secondComma).toInt();
      int green = command.substring(secondComma + 1, thirdComma).toInt();
      int blue  = command.substring(thirdComma + 1).toInt();

      setRGBColor(red, green, blue);
    } else {
      Serial.println("Error: Malformed RGB command");
    }
  }
}


// --------------------------------------------------------------
// Function to Control Single Servo | Command: ServoControl | SC,X,Angle
void servoControlMessage(String input) {
  // Parse the command for individual servo control
  int commaIndex1 = input.indexOf(',');
  int commaIndex2 = input.indexOf(',', commaIndex1 + 1);

  if (commaIndex1 != -1 && commaIndex2 != -1) {
    String servoIdStr = input.substring(commaIndex1 + 1, commaIndex2);
    String angleStr = input.substring(commaIndex2 + 1);
    int servoId = servoIdStr.toInt();
    int angle = angleStr.toInt();

    // Validate the servo angle
    if (angle >= 0 && angle <= 180) {
      Serial.print("Set servo ");
      Serial.print(servoId);
      Serial.print(" to ");
      Serial.print(angle);
      Serial.println(" degrees");
      if (servoId >= 0 && servoId <= 3) { Grip.customServoAngle(servoId, angle); } // Inside ArmGrip Class
      else if (servoId == camServoChannel) { camServo.setAngle(angle); } // Camera Servo
      else if (servoId == ballStorageServoChannel) { ballStorageServo.setAngle(angle); } // Ball Storage Servo
      
    } else {
      Serial.println("Invalid angle.");
    }
  } else {
    Serial.println("Invalid command format. Use SC,R,Angle");
  }
}


// --------------------------------------------------------------
// Function to handle ToF read commands | Format: ToFX,Index (1 to 5)
void tofControlMessage(String input) {
  int commaIndex = input.indexOf(',');

  if (commaIndex != -1) {
    String indexStr = input.substring(commaIndex + 1);
    int sensorIndex = indexStr.toInt();

    // Read and print the corresponding sensor value
    switch (sensorIndex) {
      case 1:
        //Serial.print("Back Right: ");
        Serial.println(myToFs.getBackRight());
        break;
      case 2:
        //Serial.print("Front Right: ");
        Serial.println(myToFs.getFrontRight());
        break;
      case 3:
        //Serial.print("Front Center: ");
        Serial.println(myToFs.getFrontCenter());
        break;
      case 4:
        //Serial.print("Front Left: ");
        Serial.println(myToFs.getFrontLeft());
        break;
      case 5:
        //Serial.print("Back Left: ");
        Serial.println(myToFs.getBackLeft());
        break;
      default:
        Serial.println("Invalid ToF sensor index. Use 1 to 5.");
        break;
    }
  } else {
    Serial.println("Invalid ToF command format. Use ToFX,Index (1-5)");
  }
}


// --------------------------------------------------------------
// Function to control the light brightness using PWM | Format: LX,0 to LX,255
void lightControlMessage(String input) {
  int commaIndex = input.indexOf(',');

  if (commaIndex != -1) {
    String pwmValueStr = input.substring(commaIndex + 1);
    int pwmValue = pwmValueStr.toInt();

    // Validate the PWM value (between 0 and 255)
    if (pwmValue >= 0 && pwmValue <= 255) {
      //Serial.print("Setting light brightness to: ");
      //Serial.println(pwmValue);
      
      // Set the PWM value to control brightness
      analogWrite(robotLight, pwmValue);
    } else {
      Serial.println("Invalid PWM value. Please provide a value between 0 and 255.");
    }
  } else {
    Serial.println("Invalid command format. Use LX,Value (0-255)");
  }
}


// --------------------------------------------------------------
// Function to Control Single Servo | Command: ServoControl | SC,X,Angle
void servoFreeControl(String input) {
  // Parse the command for individual servo control
  int commaIndex1 = input.indexOf(',');
  int commaIndex2 = input.indexOf(',', commaIndex1 + 1);

  if (commaIndex1 != -1 && commaIndex2 != -1) {
    String servoIdStr = input.substring(commaIndex1 + 1, commaIndex2);
    String situationStr = input.substring(commaIndex2 + 1);
    int servoId = servoIdStr.toInt();

    // Validate the servo angle
    if ( situationStr == "F") {
      //Serial.print("Set servo ");
      //Serial.print(servoId);
      //Serial.println(" to Free Mode");

      if (servoId < 0) { Grip.freeAllServos(); } // -1
      else if (servoId >= 0 && servoId <= 3) { Grip.freeXServo(servoId); } // Inside ArmGrip Class
      else if (servoId == camServoChannel) { camServo.freeServo(); } // Camera Servo
      else if (servoId == ballStorageServoChannel) { ballStorageServo.freeServo(); } // Ball Storage Servo
      
    } else {
      Serial.println("Invalid Mode (Only Free Available).");
    }
  } else {
    Serial.println("Invalid command format. Use SC,R,Free");
  }
}

// --------------------------------------------------------------
// Function to Control Single Servo | Command: ServoControl | SC,X,Angle
void ledBlinkController() {
  ledT1 = ledT0 + ledTimeInterval;
  if (millis() >= ledT1) {
    ledState = !ledState;
    if (ledState == true) {
      digitalWrite(LED_BUILTIN, HIGH);
    }
    else {
      digitalWrite(LED_BUILTIN, LOW);
    }
    ledT0 = ledT1;
  }
}


void setRGBColor(int red, int green, int blue) {
  digitalWrite(redLed, red);
  digitalWrite(greenLed, green);
  digitalWrite(blueLed, blue);
}

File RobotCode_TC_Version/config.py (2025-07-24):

# -------- Robot Configurations -------- 

print("Robot Configurations: \t \t OK")

# Is it DEBUG?
silverDatasetCollectionMode = False
victimDatasetCollectionMode = False
computerOnlyDebug = False # True for computer only, False for robot
gamepadLoopRun = True # False for score runs
DEBUG = False
softDEBUG = True
serialSoftDEBUG = False #True
pickVictimSoftDEBUG = True
LOPOverride = False # If True, LOP state will be updated virtually
LOPVirtualState = True
MotorOverride = False # If True, the robot will not move

# Camera Angle variables
CAMERA_LINE_ANGLE = 30
CAMERA_EVAC_ZONE_ANGLE = 70

# Serial Port Vars
SERIAL_PORT = '/dev/ttyACM0'
BAUD_RATE = 115200

# Buzzer Delay
buzzerONMs = 100
buzzerOffMs = 5000
buzzerState = False

# Time Delays
lineDelayMS = 20 # Frame Rate = 40 FPS
controlDelayMS = 20 # 40 Hz
serialDelayMS = 10 # 100 Hz
dataRequestDelayMS = 50 # 20 Hz
intersectionMaxTime = 1.000 #s

# Line Vars
redLineStopTime = 9.0 # s
default_crop=0.45
turn_crop=0.75
SILVER_ANGLE_THRESHOLD = 90
SILVER_CENTER_THRESHOLD = 0.20
SILVER_CLOSE_THRESHOLD = 0.40
GAP_CORRECTION_TIMEOUT = 5 # s
ANGLE_THRESHOLD = 10.0  # degrees
SEESAW_RATE_THRESHOLD = 85 # degrees per second - Requires calibration
ROBOT_CLOSE_TO_WALL_DISTANCE = 150 # mm
PARALLEL_TOF_THRESHOLD = 65 # mm
OPENING_THRESHOLD_SIDE = 300  # mm
OPENING_THRESHOLD_FRONT = 1000  # mm
# Constants for gap correction state
GAP_IDLE = 0
GAP_CORRECTING = 1
GAP_ALIGNED = 2
GAP_TIMEOUT = 3

# Color Configs
blackThreshold = 55
black_top_threshold_percentage = 0.4
black_min = [0, 0, 0]
black_max_normal_top = [82, 83, 30]
black_max_normal_bottom = [180, 90, 50]
#green_min = [50, 95, 40]    # 58, 95, 39 Night | 126, 94, 145 Day
#green_max = [100, 255, 255] # 98, 255, 255 Night | 155, 130, 180 Day
green_min = [50, 120, 70] # 50, 95, 40 # 40, 75, 35
green_max = [100,255,200] # 100, 255, 255 # 90, 255, 145
red_min_1 = [0, 100, 90]
red_max_1 = [10, 255, 255]
red_min_2 = [170, 100, 100]
red_max_2 = [180, 255, 255]

evacZoneGreenMin = [35, 100, 15]
evacZoneGreenMax = [95, 255, 115]
evacZoneRedMin_1 = [0, 100, 90]
evacZoneRedMax_1 = [10, 255, 255]
evacZoneRedMin_2 = [170, 100, 100]
evacZoneRedMax_2 = [180, 255, 255]

# Constants for speed factors and motor default values
delayTimeMS = 10
MAX_DEFAULT_SPEED = 2000
MIN_DEFAULT_SPEED = 1600 # Gamepad only?!
MIN_GENERAL_SPEED = 1000
DEFAULT_STOPPED_SPEED = 1520
DEFAULT_FORWARD_SPEED = 1600
DEFAULT_BACKWARD_SPEED = 1200
ESC_DEADZONE = 50
SPEED_STEP = 25
FACTOR_STEP = 25
MAX_SPEED_FACTOR_LIMIT = 500
MIN_SPEED_FACTOR_LIMIT = 50

# Variables that can be updated
maxSpeedFactor = 250
reverseSpeedFactor = -100
defaultSpeed = 1850

# Motor Vars
speedFactor = 0
KP = 1.8 #1.50
KD = 2.0 #2.05
KI = 0.0
KP_THETA = 140 # 407 = 1280/3.1415
Kp_distance = 2.3 # Kp for exiting the evac zone
Kp_angle = 1.2 # Kp for exiting the evac zone angle to the wall

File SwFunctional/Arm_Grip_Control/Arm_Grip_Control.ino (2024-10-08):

//#include <Wire.h>
//#include <Adafruit_PWMServoDriver.h>
#include "ArmGrip.h"

// PCA I2C Pins
const int sdaPin = 4;
const int sclPin = 5;

// Define channels for servos
const int leftHandServo = 0; // Channel 0 for the left hand servo
const int rightHandServo = 1; // Channel 1 for the right hand servo
const int leftArmServo = 2; // Channel 2 for the left arm servo
const int rightArmServo = 3; // Channel 3 for the right arm servo


// Servo positions
int defPosRH = 180; // Default (Open) position for right servo
int defPosLH = 8;  // Default (Open) position for left servo
int PosRH = defPosRH; // Current Pos right servo
int PosLH = defPosLH; // Current Pos left servo
int clPosRH = 130;   // Close position for right servo
int clPosLH = 50;   // Close position for left servo

//Create Object and Assign Values
ArmGrip Grip(sdaPin, sclPin, rightHandServo, leftHandServo);

void setup ()
{
  pinMode(LED_BUILTIN, OUTPUT);
  Serial.begin(9600);
  Grip.defineHandPositions(defPosRH, defPosLH, clPosRH, clPosLH);
  Grip.setServoAngle(0, 40);
}

void loop () 
{
  Serial.println("Alive");
  digitalWrite(LED_BUILTIN, HIGH);  // turn the LED on (HIGH is the voltage level)
  delay(500);                      // wait for a second
  digitalWrite(LED_BUILTIN, LOW);   // turn the LED off by making the voltage LOW
  delay(500); 
}


/*
// Create the PCA9685 object
Adafruit_PWMServoDriver pwm = Adafruit_PWMServoDriver();

// Define servo positions
#define SERVOMIN  150 // Minimum pulse length count (out of 4096)
#define SERVOMAX  600 // Maximum pulse length count (out of 4096)

// Define channels for servos
const int leftHandServo = 0; // Channel 0 for the left hand servo
const int rightHandServo = 1; // Channel 1 for the right hand servo
const int leftArmServo = 2; // Channel 2 for the left arm servo
const int rightArmServo = 3; // Channel 3 for the right arm servo


// Servo positions
int defPosRH = 180; // Default (Open) position for right servo
int defPosLH = 8;  // Default (Open) position for left servo
int PosRH = defPosRH; // Current Pos right servo
int PosLH = defPosLH; // Current Pos left servo
int clPosRH = 130;   // Close position for right servo
int clPosLH = 50;   // Close position for left servo

void setup() {
  Serial.begin(9600);
  //Wire.setSDA(16); // Set SDA to GPIO 16
  //Wire.setSCL(17); // Set SCL to GPIO 17
  Wire.begin();    // Initialize I2C with the specified pins
  pwm.begin();
  pwm.setPWMFreq(60);  // Analog servos run at ~60 Hz updates

  // Initialize servos to default positions to avoid shaking
  setServoAngle(rightHandServo, defPosRH);
  setServoAngle(leftHandServo, defPosLH);
  setServoAngle(rightArmServo, 0);
  setServoAngle(leftArmServo, 180);

  Serial.println("Enter the command (S0, S1, or S3,R,Angle) to move the servo:");
}

void setServoAngle(int servoNum, int angle) {
  int pulseLen = map(angle, 0, 180, SERVOMIN, SERVOMAX);
  pwm.setPWM(servoNum, 0, pulseLen);
}

void loop() {
  if (Serial.available() > 0) {
    String input = Serial.readStringUntil('\n');  // Read the input from the serial monitor
    input.trim();  // Remove any leading/trailing whitespace
    Serial.println(input);  // Echo the input back to the serial monitor

    // Check if the entered command is valid
    if (input == "S0") {
      Serial.println("Open Hand");
      setServoAngle(rightHandServo, defPosRH);
      setServoAngle(leftHandServo, defPosLH);
      PosRH = defPosRH;
      PosLH = defPosLH;
    } 
    else if (input == "S1") {
      Serial.println("Close Hand");
      setServoAngle(rightHandServo, clPosRH);
      setServoAngle(leftHandServo, clPosLH);
      PosRH = clPosRH;
      PosLH = clPosLH;
    } 
    else if (input == "S2") {
      Serial.println("Right Side");
      setServoAngle(rightHandServo, 170);
      setServoAngle(leftHandServo, 85);
      PosRH = defPosRH;
      PosLH = 80;
    }
    else if (input == "S3") {
      Serial.println("Left Side");
      setServoAngle(rightHandServo, 87);
      setServoAngle(leftHandServo, 8);
    }
    else if (input.startsWith("S4,")) {
      // Parse the command for individual servo control
      int commaIndex1 = input.indexOf(',');
      int commaIndex2 = input.indexOf(',', commaIndex1 + 1);

      if (commaIndex1 != -1 && commaIndex2 != -1) {
        String servoIdStr = input.substring(commaIndex1 + 1, commaIndex2);
        String angleStr = input.substring(commaIndex2 + 1);

        int servoId = servoIdStr.toInt();
        int angle = angleStr.toInt();

        // Validate the servo ID and angle
        if (angle >= 0 && angle <= 180) {
          Serial.print("Set servo ");
          Serial.print(servoId);
          Serial.print(" to ");
          Serial.print(angle);
          Serial.println(" degrees");
          setServoAngle(servoId, angle);
        } else {
          Serial.println("Invalid angle.");
        }
      } else {
        Serial.println("Invalid command format. Use S3,R,Angle");
      }
    }
    else if (input == "A0") {
      setServoAngle(rightArmServo, 0);
      setServoAngle(leftArmServo, 180);
    }
    else if (input == "A1") {
      setServoAngle(rightArmServo, 180);
      setServoAngle(leftArmServo, 0);
    }
    else {
      Serial.println("Not a command. Input S0, S1, or S3,R,Angle!");
    }
  }
}
*/

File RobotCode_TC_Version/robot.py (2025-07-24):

# -------- Robot Actuators/Sensors -------- 
import time
import random
from gpiozero import Button
import numpy as np

from config import *
from utils import *
from line_cam import camera_x, camera_y
from mp_manager import *


printConsoles("Robot Functions: \t \t OK")

# Situation Vars:
#objective = "Follow Line"
lastTurn = "Straight"
rotateTo = "right" # When it needs to do 180 it rotates to ...
followingSide = "right" # When it needs to rotate to the wall it follows this side (evac zone)
inGap = False
lastLineDetected = True  # Assume robot starts detecting a line
gapCorrectionStartTime = 0

pickSequenceStatus = "goingToBall" #goingToBall, startReverse, lowerArm, moveForward, pickVictim
findVictimStatusLoop = "rotating"
pickVictimType = "none"
dumpedAliveVictims = False
dumpedDeadVictims = False
dropSequenceStatus = "searchGoCorner" #searchGoCorner, startReverse, do180, goBackwards, dropVictim
wiggleStage = 0
exitSequenceStatus = "goToWall" #rotateToWall, navigateCloseToWall, turnCornerTimeout, TurnToExit, validatingExit, Exit
nextSequenceStatus = "none"
openingAhead = False
foundUnexpectedExit = False
gapSequenceStatus = "cameraUp" # cameraUp, followLine, cameraDown, done

# Loop Vars
pendingCommandsConfirmation = []

# Pin Definitions
SWITCH_PIN = 14
switch = Button(SWITCH_PIN, pull_up=True)  # Uses internal pull-up

# Motor Vars
M1 = M2 = 1520 # Left - Right
oldM1 = oldM2 = M1
error_x = errorAcc = lastError = 0
avoidingStuck = False
pitch = 0
lastPitch = None
lastPitchTime = None
pitchRateArray = createEmptyTimeArray()

# Camera Servo Angle
camServoAngle = -1

# Sensor Vars
Accel_X_Array = createEmptyTimeArray()
Accel_Y_Array = createEmptyTimeArray()
Accel_Z_Array = createEmptyTimeArray()
accelAverage_X = accelAverage_Y = accelAverage_Z = 0

Gyro_X_Array = createEmptyTimeArray()
Gyro_Y_Array = createEmptyTimeArray()
Gyro_Z_Array = createEmptyTimeArray()
gyroAverage_X = gyroAverage_Y = gyroAverage_Z = 0

Temp_Array = createEmptyTimeArray()
tempAverage = 0

Tof_1_Array = createEmptyTimeArray()
Tof_2_Array = createEmptyTimeArray()
Tof_3_Array = createEmptyTimeArray()
Tof_4_Array = createEmptyTimeArray()
Tof_5_Array = createEmptyTimeArray()
tofAverage_1 = tofAverage_2 = tofAverage_3 = tofAverage_4 = tofAverage_5 = 0


timer_manager = TimerManager()

# Interpret CLI Commands
def CLIinterpretCommand(mpMessage):
    global MotorOverride, LOPOverride, LOPVirtualState

    message = mpMessage.value

    if message == "exit": # Exit command
        printConsoles("Exiting...")
        terminate.value = True
        return
    elif message == "list":
        printConsoles("Command List: ")
        printConsoles(f"  - exit")
        printConsoles(f"  - vars")
        printConsoles(f"  - nextImage")
        """printConsoles(f"  - Drop Alive")
        printConsoles(f"  - Drop Dead")
        printConsoles(f"  - Close Ball Storage")
        printConsoles(f"  - Pick Alive")
        printConsoles(f"  - Pick Dead")
        printConsoles(f"  - Camera Evacuation")
        printConsoles(f"  - Camera Line")"""
        printConsoles(f"  - MotorOverride <0 or 1>")
        printConsoles(f"  - LOPOverride <0 or 1>")
        printConsoles(f"  - LOPState <0 or 1>")
        printConsoles(f"  - Objective <FL or EZ>")
        printConsoles(f"  - ZoneStatus <notStarted, begin, entry, findVictims, goToBall, depositRed, depositGreen, exit>")
        printConsoles(f"  - cameraFree <15-90>")
        printConsoles(f"  - setLights <0 or 1>")
        printConsoles(f"  - setCustomLights <0-255>")
        printConsoles(f"  - rgbLed <R> <G> <B>  (0-255 each)")
        printConsoles(f"  - PV <Alive|Dead> [step]")
        printConsoles(f"  - DV <Alive|Dead>")
        printConsoles(f"  - BC")
        printConsoles(f"  - SaveFrame <0 or 1>")
    elif message == "vars":
        printConsoles(f"  - LOPOverride: {LOPOverride}")
        printConsoles(f"  - LOPVirtualState: {LOPVirtualState}")
        printConsoles(f"  - MotorOverride: {MotorOverride}")
        printConsoles(f"  - Objective: {objective.value}")
        printConsoles(f"  - Zone Status: {zoneStatus.value}")
        printConsoles(f"  - Zone Start Time: {round(zoneStartTime.value, 3)}")
        printConsoles(f"  - Zone Duration: {round(time.perf_counter() - zoneStartTime.value, 3) if zoneStartTime.value != -1 else 'Not Started'}")
        printConsoles(f"  - Picked {pickedUpAliveCount.value} Victim(s) and {pickedUpDeadCount.value} Victims(s)")
        printConsoles(f"  - Rescued {dumpedAliveCount.value} Victim(s) and {dumpedDeadCount.value} Victims(s)")
    elif message == "": #Next Image
        printDebug("Next Image", False)
        updateFakeCamImage.value = True
    elif message.startswith("MotorOverride"):
        try:
            MotorOverride = bool(int(message.split()[1]))
            printConsoles(f"Motor Override set to {MotorOverride}")
        except (ValueError, IndexError):
            printConsoles("Invalid motorOverride command. Use 'motorOverride <0 or 1>'")
    elif message.startswith("LOPOverride"):
        try:
            LOPOverride = bool(int(message.split()[1]))
            printConsoles(f"LOP Override set to {LOPOverride}")
        except (ValueError, IndexError):
            printConsoles("Invalid LOPOverride command. Use 'LOPOverride <0 or 1>'")
    elif message.startswith("LOPState"):
        try:
            LOPVirtualState = bool(int(message.split()[1]))
            printConsoles(f"LOP State set to {LOPVirtualState}")
            if not LOPOverride:
                printConsoles(f"LOP Override is OFF. LOP State will not change anything.")
                printConsoles(f"Run LOPOverride <1> to be able to change LOP State.")
        except (ValueError, IndexError):
            printConsoles("Invalid LOPState command. Use 'LOPState <0 or 1>'")
    elif message.startswith("Objective"):
        try:
            _, objectiveCode = message.split(maxsplit=1)
            objectiveCode = objectiveCode.strip().upper()

            if objectiveCode == "FL":
                objective.value = "follow_line"
                cameraDefault("Line")
                printConsoles("Objective set to FOLLOW LINE.")
            elif objectiveCode == "EZ":
                objective.value = "zone"
                zoneStatus.value = "begin"
                cameraDefault("Zone")
                printConsoles("Objective set to ZONE.")
            else:
                printConsoles(f"Unknown Objective '{objectiveCode}'. Use 'FL' or 'EZ'.")
        except (ValueError, IndexError):
            printConsoles("Invalid Objective command. Use 'Objective FL' or 'Objective EZ'.")
    elif message.startswith("ZoneStatus"):
        try:
            _, zoneCode = message.split(maxsplit=1)
            zoneCode = zoneCode.strip()

            allowedZoneStatuses = [
                "notStarted", "begin", "entry", "findVictimsSetup", "findVictims",
                "goToBall", "depositRed", "depositGreen", "exit"
            ]
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

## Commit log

2024-10-10 Created Encoder Test specific for 1 Motor
2024-10-10 Fixed Error with VS Compiling (modified arduino.json)
2024-10-10 Cleaned the Code for only 1 Motor
2024-10-10 Got a decent output from encoders (saved pictures) Prior to Interrupts
2024-10-10 Works "Well" for 1 motor, but still requires further testing to verify. Incompatible with multiple motors...
    [Motor.cpp]
2024-10-14 Created a second encoder motor test file/folder
2024-10-14 Fixed Workspace Program (not sending correct file to pico)
    [Encoder_1_Motor_Test_2.ino, Motor.cpp]
2024-10-14 Tried to Implement .getRPM() ; realised that pulses counts for multiple motors is *****
2024-10-14 Got Fully Functional Motor Control through Serial (No Encoders, ready for RPI control) Encoder_1_Motor_Test_2.ino is broken
    [Encoder_1_Motor_Test_2.ino, Motor.cpp]
2024-11-14 Created Updated Implementation Folder (Motor + Arm)
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2025-01-25 Francisco: Merged Pico Code into one File (Untested)
2025-01-25 Francisco: Added Camera and Ball Storage Servos Entries Fixed Compiler Errors
    [ArmGrip.cpp, Pico_Code.ino, myServo.cpp]
2025-01-25 Francisco: Added More Servo Commands Place Holders
2025-01-25 Francisco: Added Led Blink every interval (set to 1s)
2025-01-26 Francisco: Added "Camera Check" in camera specific functions inside myServo.h
2025-01-26 Francisco: Added "Ball Storage Check" in Ball Storage Servo specific functions inside myServo.cpp
2025-01-26 Francisco: Created variables for default positions for Camera and Ball Storage Servos
2025-01-27 Francisco: Added Error message for specific servo functions (camera/ball storage servos)
    [myServo.cpp]
2025-01-27 Francisco: Added Missing Error
    [myServo.cpp]
2025-01-27 Francisco: Completed Ball Storage Servo Functions in myServo.cpp with calibrated values (BC 90, DD 30, DA 150)
2025-01-27 Francisco: Completed Camera Servo Functions in myServo.cpp with calibrated angles for lineFollowing and EvacuationZone
2025-01-28 Francisco: Finished calibrating all servo values
2025-01-28 Francisco: Added Protocol for RPi to check if Pico is ALIVE
2025-01-28 Francisco: Fixed Slow Moving Arm Function Bug
    [ArmGrip.cpp]
2025-01-28 Francisco: Added Functionality to stop servo "shaking", now able to free servo from trying to hold the position (.freeServo()), for camServo and ballStorageServo
2025-01-28 Francisco: Implemented Free Servo Commands in Setup to prevent initial shaking
    [Pico_Code.ino]
2025-01-29 Francisco: Increased minimum motor speed to 1700 to improve reliability (motor stall)
    [Pico_Code.ino]
2025-01-30 Francisco: Decreased RPi 5 loop iteration time to 10ms, which corresponds to 100Hz
2025-02-03 Francisco: Fixed "no arm down before victim pick" bug; Set Free servos in ball storage
    [main.py]
2025-02-04 Francisco: Fixed Motor Pins on Pico_Code.ino
    [Pico_Code.ino, main.py]
2025-02-04 Francisco: Fixed Motor Pins
    [Pico_Code.ino]
2025-02-04 Francisco: Solved switched motor inputs for forward motion
    [main.py]
2025-02-04 Francisco: Fixed "Object not callable" ser.in_waiting() to ser.in_waiting
    [main.py]
2025-02-04 Francisco: Fixed chr(c) in readSerial()
    [main.py]
2025-02-04 Francisco: Added debug print for not functional "Ok" receiver
2025-02-04 Francisco: Replaced received == response to response in received for conditional improvement
    [main.py]
2025-02-04 Francisco: Removed prints from RPi Pico ArmGrip for further wait Response testing
2025-02-04 Francisco: Removed further Pico prints
2025-02-04 Francisco: Fixed interpreter error: takes 3 positional arguments, only 2 were...
    [main.py]
2025-02-04 Francisco: Added another print for debugging on RPI sendSerialResponse
2025-02-04 Francisco: Found bug in readSerial RPi/main.py (neglecting serial port) if ser.in_waiting <= 0: instead of >
    [main.py]
2025-02-04 Francisco: Attempt to solve motor uncontrollable after arm/ball commands
2025-02-04 Francisco: --Test-- Deleted ser.flush() caused random motor movements, using reset_input_buffer()
    [main.py]
2025-02-05 Francisco: Added OLD Pico Code version for testing purposes
2025-02-05 Francisco: Fixed test bug
    [main.py]
2025-02-05 Francisco: Fixed bug in test
    [main.py]
2025-02-05 Francisco: Attempt to fix logic problem
    [main.py]
2025-02-05 Francisco: Trying to fix git??
    [main.py]
2025-02-05 Francisco: Stable Release: Proper Command waiting lists (works with arm and ball storage operations)
2025-02-10 Francisco: Fixed motor not stopping bug
    [gamepad.py]
2025-02-10 Francisco: Fixed compiler error
    [gamepad.py]
2025-02-10 Francisco: Removed duplicate code from robot.py arm functions
2025-02-10 Francisco: Added Camera Interactions through gamepad.py
2025-02-10 Francisco: --Test-- Fixing Compiler Error
    [gamepad.py]
2025-02-10 Francisco: --Test-- Fixing Bug
    [robot.py]
2025-02-10 Francisco: Fixed interpretMessage(), copied properly previous stableRelease
    [robot.py]
2025-02-10 Francisco: Removed Not needed debug prints
2025-02-10 Francisco: Fixed double first command sending bug
    [robot.py]
2025-02-10 Francisco: New Stable Release, without duplicate code, and camera gamepad interface implemented
2025-02-10 Francisco: Removed Auto ESC arming (attempt to fix disarming)
    [Pico_Code.ino]
2025-02-10 Francisco: Added delay for camera servo to get to desire position
2025-02-10 Francisco: Implemented initial setup commands in RPi (ESC Arming and Servo "Homing")
2025-02-10 Francisco: Attempt to only allow for one motor arm per pico "life"
2025-02-12 Francisco: Fixed variable definition problem
    [gamepad.py, main.py]
2025-02-15 Francisco: Camera working -low quality through ssh
2025-02-16 Francisco: Tested successfully LoP switch on/off
2025-02-17 Francisco: Functional with no Buzzer
    [gamepad.py]
2025-02-22 Francisco: Only LoP Switch Attempt
2025-02-22 Francisco: Created new Stable Release with LoP Switch
2025-03-01 Francisco: Ready for frames collection
2025-03-02 Francisco: Fixing previous commit
    [Line_Cam.py]
2025-03-03 Francisco: Fixed bad return to stable release IP2
    [gamepad.py, line_cam.py, main.py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]
2025-03-04 Francisco: Calibrated maxlinewidth and blackTop
2025-03-11 Francisco: Increased Line Frame Rate to 40FPS
2025-04-01 Francisco: Fixed Git on Rpi
    [line_cam.py, main.py, mp_manager.py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]
2025-04-03 Francisco: Fixing lack of line_cam file
    [line_cam.py]
2025-04-17 Francisco: One More fix...
    [line_cam.py]
2025-04-20 Francisco: Created I2C Scanner
2025-04-20 Francisco: ToF Sensors Integration Tests
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2025-04-26 Francisco: Added a command line reader thread
2025-04-26 Francisco: New CLI commands exit, list, motor, LOP
2025-04-26 Francisco: MotorOverride is now funcitonal
2025-04-27 Francisco: Created base functions for sensor data arrays
2025-05-10 Francisco: Increased Time Loop + Debug Message Pico
2025-05-17 Francisco: Debugging and slight fixes need to deposit functions
    [line_cam.py, mp_manager.py, robot.py]
2025-05-17 Francisco: Made serial prints selective in config. Added additional command based debug information
2025-05-18 Francisco: Fixed double drop bug. NeedDeposit still requires more checking on safeties.
    [config.py, line_cam.py, robot.py]
2025-05-18 Francisco: Evacuation Zone Values Calibration
2025-05-18 Francisco: Simple Pico Code Cleaning
2025-05-18 Francisco: Color Calibration Data
2025-05-19 Francisco: Created basic web socket and html page for live data streaming
2025-05-25 Francisco: Added more debug features to the Web Socket
2025-06-02 Francisco: Updated pins for new PCB
2025-06-02 Francisco: Created more detailed I2C Scanner with bus definition
2025-06-04 Francisco: Code compatible with IMU data
2025-06-06 Francisco: Pico Compatible with IMU, Robot Lights and RGB Led
2025-06-07 Francisco: ToF Integrated to Pico Code
2025-06-07 Francisco: IMU data class clean up
2025-06-07 Francisco: Final command to get IMU and ToF Data
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2025-06-08 Francisco: Not Initialized Sensors Bug Fix (now Independent)
    [IMU.cpp]
2025-06-08 Francisco: Fixed 2 Line Sensor Data Bug
    [Pico_Code.ino]
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2025-06-08 Francisco: Updated HTML Robot Page to contain IMU and ToF data
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2025-06-08 Francisco: Fixed sensor data print bug
    [Pico_Code.ino]
2025-06-08 Francisco: Fixed ToF Hang Bug
    [Pico_Code.ino, ToF.cpp]
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2025-06-13 Francisco: Added Stuck Detection with Structural Similarity
    [WebSocket_Server.py, line_cam.py, mp_manager.py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]
2025-07-01 Francisco: Fixed bug not going forward on zone after victim drop
    [robot.py]
2025-07-01 Francisco: Added camServoAngle to have camera adjustment in ramp
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2025-07-01 Francisco: Fixed bug with pending serial loop
    [WebSocket_Server.py, config.py, line_cam.py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]
2025-07-01 Francisco: Fixed bug with double ball pickup
    [WebSocket_Server.py, line_cam.py, mp_manager.py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]
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2025-07-02 Francisco: Added silverLineDetected reset to False
    [robot.py]
2025-07-02 Francisco: Reduced stuck detection time to last 10seconds
    [line_cam.py]
2025-07-02 Francisco: Added cooldown timer for pickVictim to avoid double picks
    [line_cam.py, robot.py]
2025-07-02 Francisco: Fixed bug in interpretPoi black on both sides (wrong angle, needed to be normalized)
    [line_cam.py, robot.py]
2025-07-03 Francisco: Fixed bug with blocking sensor data request
    [mySerial.py]
2025-07-03 Francisco: Fixed bug with sensor data request v2
    [mySerial.py]
2025-07-03 Francisco: Improved sensor data parser to allow for inverted message lines
    [config.py, mySerial.py]
2025-07-03 Francisco: Reduced sensor data request delay by splitting ToF measurements
2025-07-03 Francisco: Increased victim pick cooldown (8s) to avoid double picks and silverline ready to enter is set to true if no line is detected
    [robot.py]
2025-07-03 Francisco: Removed wrong debug prints
    [robot.py]
2025-07-04 Francisco: Added average to red line detection and fixed wait time (not permanent)
    [config.py, line_cam.py, mp_manager.py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]
2025-07-04 Francisco: Implemented the use of latest victim ball detection model and fixed red line detection bug
    [line_cam.py]
2025-07-05 Francisco: Fixed bug with red line detection and calibrated seesaw detection
    [config.py, robot.py]
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2025-07-05 Francisco: Improved seesaw detection with average and calibrated times/values
2025-07-07 Francisco: entry zone fix (tof values states and angles calibration)
    [config.py, robot.py]
2025-07-07 Francisco: Fixed bugs in entry zone function
    [config.py, robot.py]
2025-07-07 Francisco: Found bug with waiting for pick timer
    [robot.py]
2025-07-08 Francisco: Developed Exiting Evac Zone procedure (control only, requires line camera loop updates)
2025-07-08 Francisco: Fixed bug with rotation speed after deposit and saving images in the wrong folder
    [line_cam.py, robot.py]
2025-07-08 Francisco: Went Back to previous AI model and fixed bug with exit aligned with wall wrong variable
    [line_cam.py, robot.py]
2025-07-08 Francisco: Added a check to avoid saying we alligned when we are not close to the wall (facing away from it)
    [robot.py]
2025-07-08 Francisco: Fixed typo in aligned condition
    [line_cam.py, robot.py]
2025-07-08 Fixed bugs with navigating close to wall (inverted signs)
    [config.py, mySerial.py, robot.py]
2025-07-09 Francisco: Pico stops motors after closing hand on the correct position
    [ArmGrip.cpp, Pico_Code.ino]
2025-07-09 Francisco: Removed duplicate line function and added area print debug
2025-07-10 Francisco: Added failsafe in case the edgetpu model fails to load (try again)
    [config.py, line_cam.py]
2025-07-10 Francisco: Improved error handling for edgetpu (reloads model)
    [line_cam.py]
2025-07-10 Francisco: Fixed intermittent bug with picking victims cooldown
    [config.py, robot.py]
2025-07-10 Francisco: Exit bug fixing
    [config.py, line_cam.py, mp_manager.py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]
2025-07-10 Francisco: Brough back sensor request data timeout (35ms)
2025-07-12 Francisco: Fixed typo in mp_manager.py
    [mp_manager.py]
2025-07-12 Francisco: Fixed "return" bug that crashed robot when picking ball
    [robot.py]
2025-07-13 Francisco: Stable Release (with full evac zone) :) Requires bug hunting for multiple evac zone entries and arm position fdix
2025-07-13 Francisco: Still functional state (upgraded Kp value, red line timer, frame max duration)
2025-07-15 Francisco: Fixed path denomination for RobotCode/line_cam.py
    [line_cam.py]
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
